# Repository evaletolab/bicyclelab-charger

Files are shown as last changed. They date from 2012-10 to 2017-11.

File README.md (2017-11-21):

# 85-110W single output battery charger

This is an opensource lithium-ion battery charger that use laptop power adapter as input.
* Further reading regarding [the bicycle manager](https://github.com/evaletolab/bicyclelab-manager)?

## Features

1. boost input from 18.5V - 4.7A to 42V (or 47.2V) with ~95% of efficiency 
2. stage charging; current control then voltage control
3. full protections: Short circuit / Overload / Over voltage / Over temperature
4. 1 LED indicator for charging status
5. BMS features; Balancing charge on each cell [TODO]
6. custom number of serial cells 5..12
7. small size, only 30x90x8mm

The PCB board charger v4.2

## The result
8S2P

## Power stage (battery charge)

This if the fourth prototype release. The purpose of this board is to manage the charge  
of a 10/11 serial lithium-ion cell with an input given by a laptop ac adapter (currently the apple magsafe1 85W). 
The software is mainly a PID control based on the MAX_POWER for the fast charge and the BATTERY_VOLTAGE for 
the constant charge. The size of the board is about 30x90mm

## Cell balancing and protection
This project is targeted for each individual cell. The purpose of this project is to make a simple cascading 
module to manage over/under voltage/temperatur for each cell. The first prototype is still not available for testing. 

1. an overvoltage measurement is triggering a passive balancing for the cell
2. TODO - implement an isolated one wire communication to broadcast,
  * undervoltage signal
  * over temperature signal
 
## License
GPL3

Copyright (c) 2012 Olivier Evalet (http://evaletolab.ch/)

Permission is hereby granted, free of charge, to any person obtaining a copy
of this software and associated documentation files (the “Software”), to deal
in the Software without restriction, including without limitation the rights
to use, copy, modify, merge, publish, distribute, sublicense, and/or sell
copies of the Software, and to permit persons to whom the Software is
furnished to do so, subject to the following conditions:

The above copyright notice and this permission notice shall be included in
all copies or substantial portions of the Software.

THE SOFTWARE IS PROVIDED “AS IS”, WITHOUT WARRANTY OF ANY KIND, EXPRESS OR
IMPLIED, INCLUDING BUT NOT LIMITED TO THE WARRANTIES OF MERCHANTABILITY,
FITNESS FOR A PARTICULAR PURPOSE AND NONINFRINGEMENT. IN NO EVENT SHALL THE
AUTHORS OR COPYRIGHT HOLDERS BE LIABLE FOR ANY CLAIM, DAMAGES OR OTHER
LIABILITY, WHETHER IN AN ACTION OF CONTRACT, TORT OR OTHERWISE, ARISING FROM,
OUT OF OR IN CONNECTION WITH THE SOFTWARE OR THE USE OR OTHER DEALINGS IN
THE SOFTWARE.

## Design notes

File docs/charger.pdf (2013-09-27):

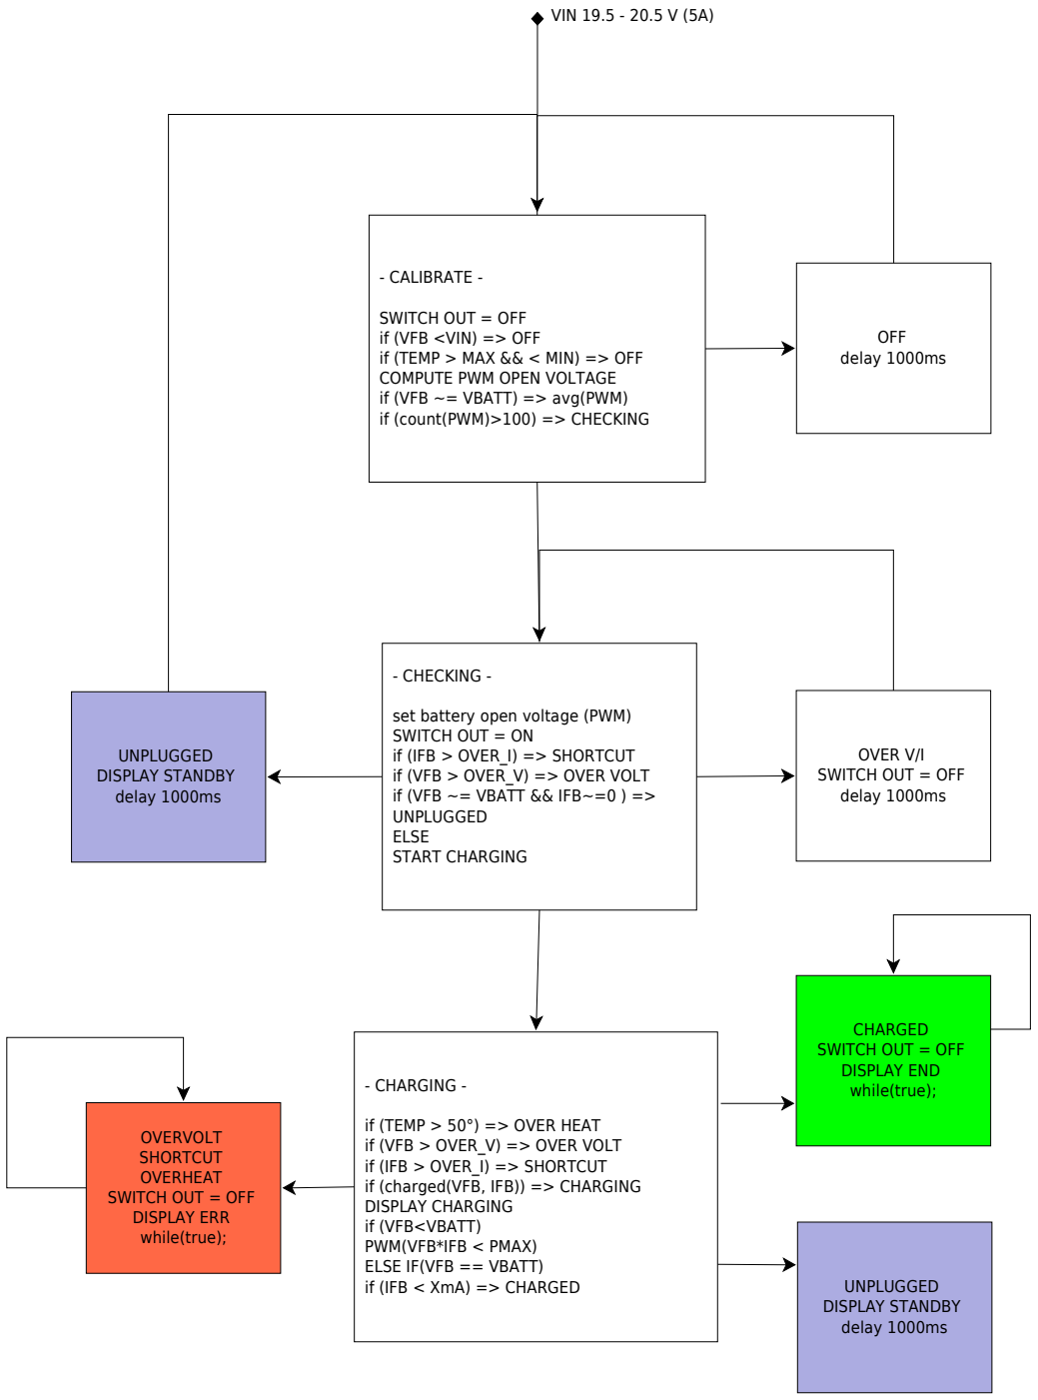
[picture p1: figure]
- CALIBRATE -; SWITCH OUT = OFF if (VFB <VIN) => OFF if (TEMP > MAX && < MIN) => OFF COMPUTE PWM OPEN VOLTAGE if (VFB ~= VBATT) => avg(PWM) if (count(PWM)>100) => CHECKING; OFF delay 1000ms; VIN 19.5 - 20.5 V (5A); - CHECKING -; set battery open voltage (PWM) SWITCH OUT = ON if (IFB > OVER_I) => SHORTCUT if (VFB > OVER_V) => OVER VOLT if (VFB ~= VBATT && IFB~=0 ) => UNPLUGGED ELSE START CHARGING; OVER V/I SWITCH OUT = OFF delay 1000ms; UNPLUGGED DISPLAY STANDBY delay 1000ms; - CHARGING -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

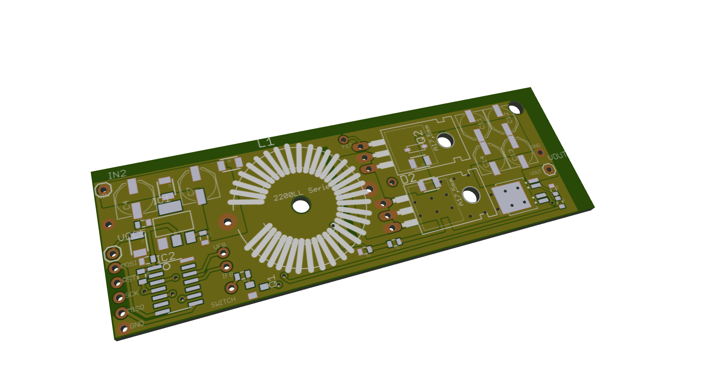
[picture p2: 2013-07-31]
hardware/bicyclelab-charger-v0.1.3d.png

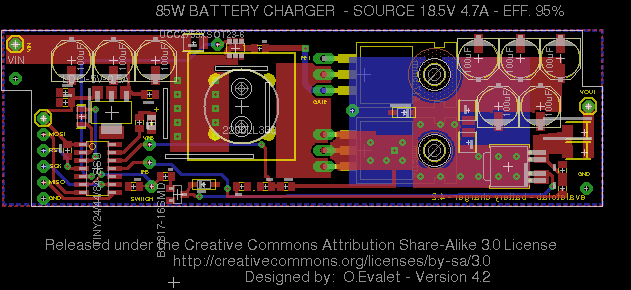
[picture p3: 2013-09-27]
hardware/bicyclelab-charger-v4.2.png

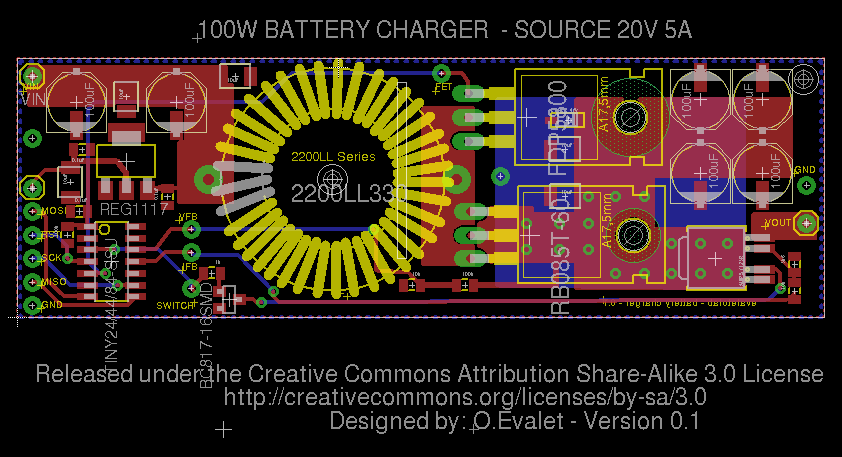
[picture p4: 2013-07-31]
hardware/bicyclelab-charger-v0.1.png

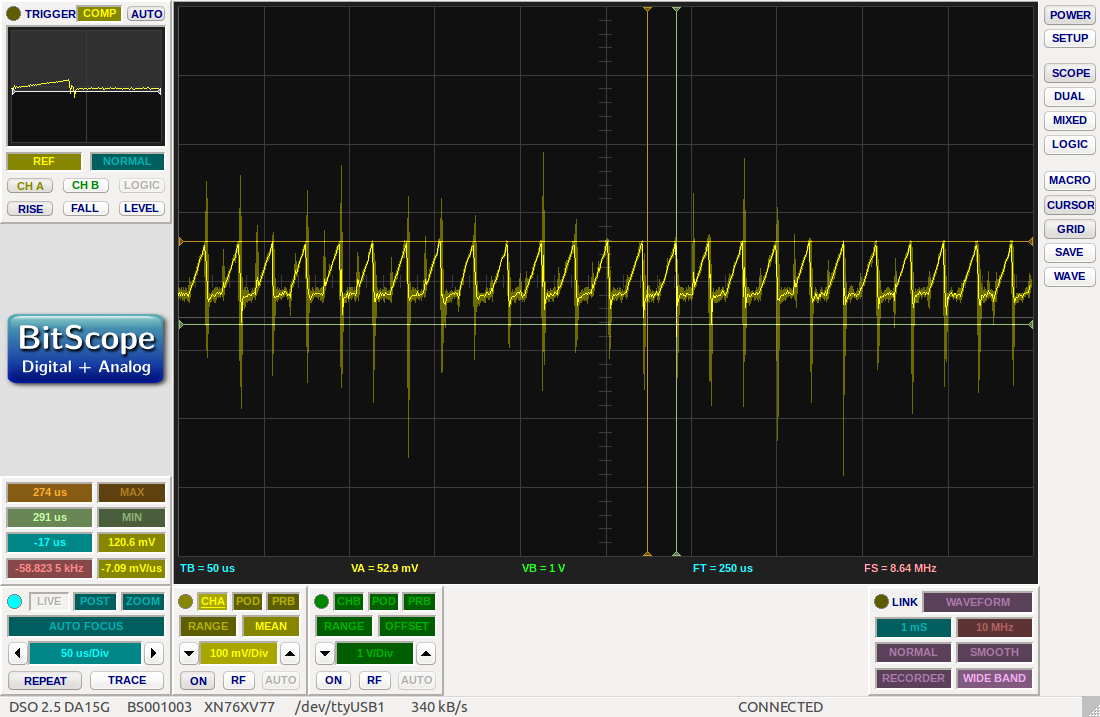
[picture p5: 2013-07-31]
docs/scope/uc1842 - isens - Capture du 2013-07-26 17:00:00.png

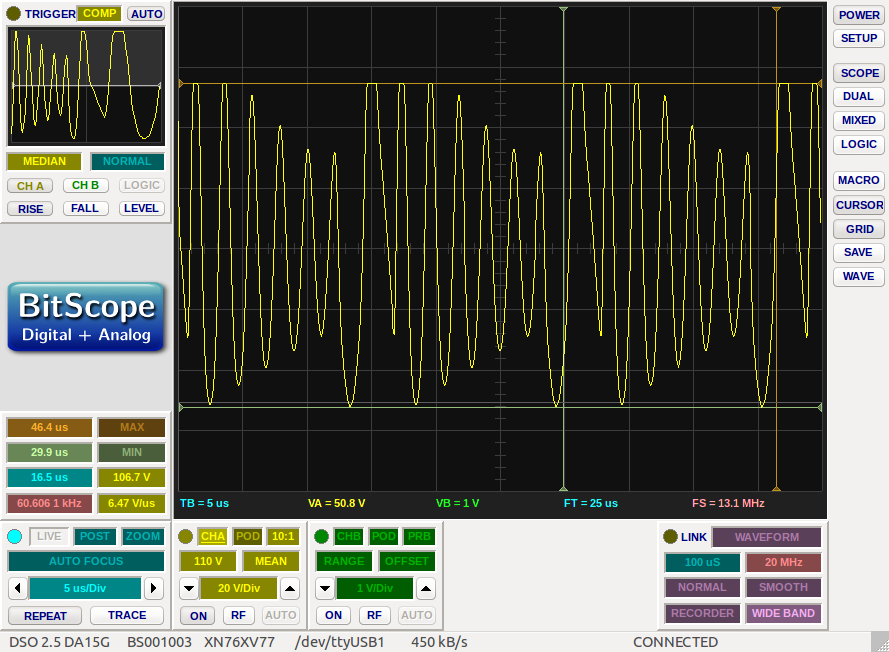
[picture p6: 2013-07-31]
docs/scope/5v - 20V - 60khz - Capture du 2013-07-24 09:50:51.png

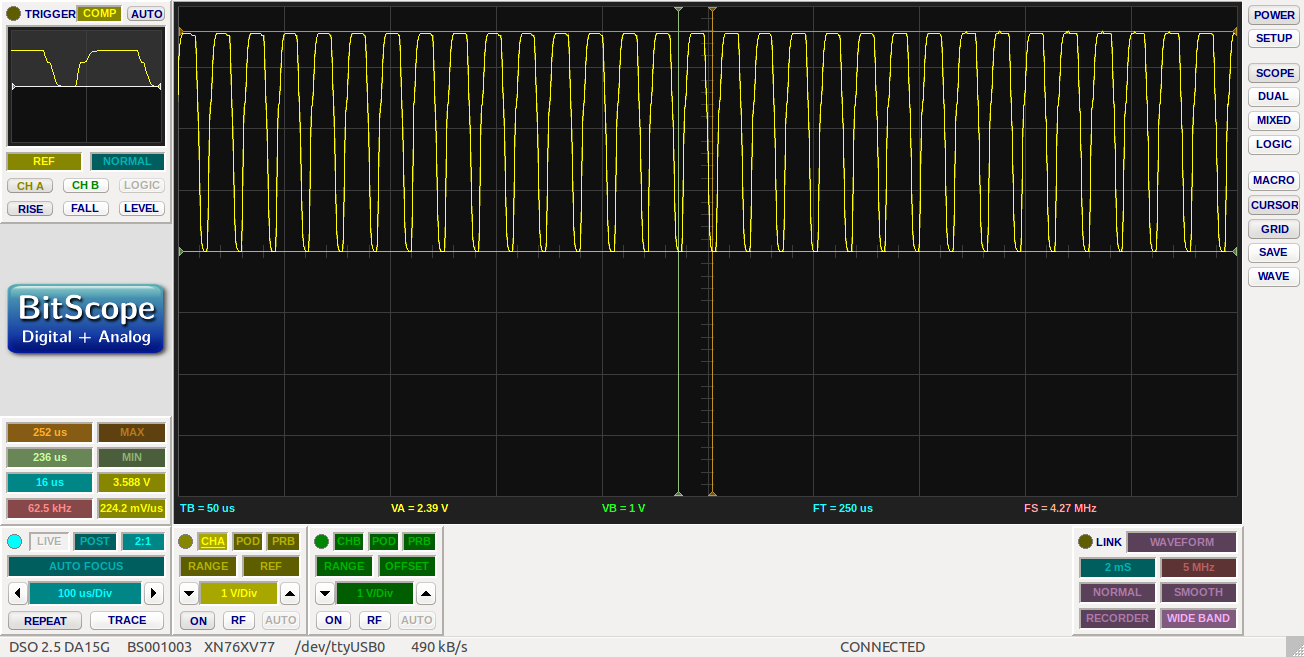
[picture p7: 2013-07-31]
docs/scope/arduino boost - gate - Capture du 2013-07-26 17:20:36.png

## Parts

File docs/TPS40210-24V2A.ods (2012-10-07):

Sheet: 20V_2A
PARAMETER |  | CONDITIONS | MIN | NOM | MAX | UNIT | STATUS
INPUT
Vin | Input voltage |  | 8 | 12 | 14 | V
Iin | Input current |  |  | 4.5 |  | A |  | Vref= | 0.700 V
 | No load I |  |  |  |  | A |  | Pfet< | 0.50 W
UV | Under voltage |  |  | 4.5 |  | V |  | RDSon< | 0.010 Ohms
OUTPUT |  |  |  |  |  |  |  | Rout= | 24.0 Ohms
Vout | Output voltage |  | 23.5 | 24 | 24.5 | V |  | Rout(max)= | 240.0 Ohms
 | Line regulation |  |  |  | 1 % |  |  | Rfb(r4)= | 16'711 Ohms
 | Load regulation |  |  |  | 1 % |  | NOMORE | Risns= | 0.012 Ohms
Vout(ripple) |  |  |  |  | 0.5 | Vpp |  | Rbias(r5)= | 1'535 Ohms
Iout | Output current | 18 =< Vin =< 24 | 0.1 | 1 | 2 | A |  | R7= | 51'100 Ohms
Iocp | Output overcurrent inception point |  | 3.5 |  |  | A |  | RC= | 261K
 | Transiant response |  |  |  |  |  |  | CC= | 100pF
 | Load step |  |  | 1 |  | A | TOFIX | Cout= | 3.6E-05 F
 | Load slew rate |  |  | 1 |  | A/us | TOFIX | C4~ | 63.5E-12 F
 | Overshoot threshold voltage |  |  | 0.5 |  | V | TOFIX | C4> | 12.7E-12 F
OTHER |  |  |  |  |  |  |  | C2= | 3.2E-09 F
Vfd | Diode Forward voltage |  |  | 0.5 |  | V
Fsw | Switching frequency |  |  | 600000 |  | Hz
Vin(ripple) |  |  |  | 0.06 |  | V
Vfb(ref) | Voltage reference for TPS40210 |  |  | 0.7 |  | V
 | Voltage reference for TPS40211 |  |  | 0.26 |  | V
n | Full load efficiency |  |  | 0.95 |  | %
Duty Cycle Estimation Dmin, Dmax |  | Adding 43V zener as secure overvoltage protection BZT52C43
Dmin= | 0.43
Dmax= | 0.67
D= | 0.55
Inductor Selection
Iripple(max)= | 1.05 | NS10155T150MNA (10x10x5.5mm) 15uH (http://ch.mouser.com/ProductDetail/Taiyo-Yuden/NS10155T150MNA/?qs=PzICbMaShUfjlUDrCZqQrFxQdiB4Wjv1sIUX92p1XCQ=) |  | 0.028
Lmin> | 9.5E-06 | IHLP3232DZER150M11 (8x9x4mm) 15uH (http://ch.mouser.com/ProductDetail/Vishay-Dale/IHLP3232DZER150M11/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) |  | 0.000015 |  | uH
L= | 10.0E-06
Iripple(VinTyp)= | 1.10 | IMPORTANT cf. Pfet | DCR(L)= | 0.0124
Iripple(Vinmin)= | 0.90
Ilrms= | 6.14 | WARNING WITH THE INDUCTOR SELECTION
Ilpeak= | 6.57
PL~= | 0.47 | THE SELECTED INDUCTOR DISSIPATES 2.2W OF POWER
Rectifier Diode Selection
Vbrmin= | 30 | the rectifier diode minimum reverse break-down voltage
Id= | 2.00
Idpeak= | 6.57
Pdmax= | 1
Output Capacitor Selection
Cout= | 0.000036 F
ESR= | 0.10 Ohms
R(esr)= | 0.06 Ohms
Input Capacitor Selection
Cin> | 0.000006 F
ESR< | 0.03 Ohms
Current Sense and Current Limit
Riflt= | 1000 Ohm
Ciflt= | 71.4E-12 | For a 1-kΩ filter resistor, 72 pF is calculated and a 100-pF capacitor is selected.
Ciflt= | 100pF
Current Sense Filter
Idrive= | 0.50 A
VISNS= | 0.15 V
Risns< | 0.019 Ohms
Risns< | 0.112 Ohms
Risns= | 0.012 Ohms
Prisns= | 0.305 W
Switching MOSFET Selection |  |  |  |  |  |  |  | FET(check the gate voltage)
Ivdd(max)= | 0.003 | IVDD is the quiescent current of the controller when enabled but not switching in A |  |  |  |  |  | FDS86540 (http://ch.mouser.com/ProductDetail/Fairchild-Semiconductor/FDS86540/) | 60V 20V 18A 5mOhm 5W
Pdiss= | 2.53 W |  |  |  |  |  |  | BSZ076N06NS3 G (http://ch.mouser.com/ProductDetail/Infineon-Technologies/BSZ076N06NS3-G/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) | 60V 20V 7mOhms 60W
Pfet< | 0.71 W | 20 mΩ is calculated to limit the conduction losses to less than .57 mW |  |  |  |  |  | FDMS86520L (http://ch.mouser.com/ProductDetail/Fairchild-Semiconductor/FDMS86520L/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) | 60V 13.2A 8.2mOhms 69W
Pfet= | 0.50 W
Qgs< | 1.3E-08 | Qgs<8,5nF
Rds(on)< | 0.010 Ohms
Feedback Divider Resistors
Vfb= | 0.7
FL(10 % Fsw)= | 30'000 Hz
Rout= | 24.0 Ohms
Rout(max)= | 240.0 Ohms
gm= | 19.19 A/V
Zout= | 0.159 Ohms
Kco= | 3.058
Kcomp= | 0.327
R4(rfb)= | 16'711 Ohms
Cfb= | 3.2E-09
Chf= | 317.47E-13
R5(rbias;r2)= | 1535.2 Ohms
R7(r1)= | 51100.0 Ohms
C2= | 3.17E-09
C2= | 4.7nF
C4~ | 63.5E-12
C4> | 12.7E-12
C4= | 47pF
R-C Oscillator (600Khz)
C3= | 100pF
R6= | 261K
Soft-Start Capacitor
Css= | 240.0E-09
For TSS = 12 ms, CSS = 240 nF. A 220-nF capacitor is selected.
Regulator Bypass
A regulator bypass (BP) capacitor of 1.0-μF is selected per the datasheet recommendation.

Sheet: Feuille2
R5=Rbias
R4=Rfb
C4=Cfb

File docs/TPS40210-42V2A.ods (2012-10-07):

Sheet: 20V_2A
PARAMETER |  | CONDITIONS | MIN | NOM | MAX | UNIT | STATUS | Vclloop(min)= | 0.010 V
INPUT |  |  |  |  |  |  |  | Rcloop= | 0.10 Ohms
Vin | Input voltage |  | 18 | 19 | 20 | V |  | L= | 11.1E-06 H
Iin | Input current |  |  | 5 |  | A |  | Vref= | 0.260 V
 | No load I |  |  |  |  | A |  | Pfet< | 0.50 W
UV | Under voltage |  |  | 4.5 |  | V |  | RDSon< | 0.012 Ohms
OUTPUT |  |  |  |  |  |  |  | Rout= | 21.0 Ohms
Vout | Output voltage |  | 41.5 | 42 | 42.5 | V |  | Rout(max)= | 420.0 Ohms
 | Line regulation |  |  |  | 1 % |  |  | Rfb(r4)= | 24'819 Ohms
 | Load regulation |  |  |  | 1 % |  | NOMORE | Risns= | 0.012 Ohms
Vout(ripple) |  |  |  |  | 0.5 | Vpp |  | Rbias(r5)= | 318 Ohms
Iout | Output current | 18 =< Vin =< 24 | 0.1 | 2 | 2.5 | A |  | R7= | 51'100 Ohms
Iocp | Output overcurrent inception point |  | 3.5 |  |  | A |  | RC= | 261K
 | Transiant response |  |  |  |  |  |  | CC= | 100pF
 | Load step |  |  | 1 |  | A | TOFIX | Cout= | 38.4E-06 F
 | Load slew rate |  |  | 1 |  | A/us | TOFIX | C4~ | 42.8E-12 F
 | Overshoot threshold voltage |  |  | 0.5 |  | V | TOFIX | C4> | 85.5E-13 F
OTHER |  |  |  |  |  |  |  | C2= | 2.1E-09 F
Vfd | Diode Forward voltage |  |  | 0.5 |  | V |  | Cin> | 10.0E-06 F
Fsw | Switching frequency |  |  | 600000 |  | Hz |  | Ciflt= | 88.2E-12 F
Vin(ripple) |  |  |  | 0.06 |  | V |  | Risns= | 0.012 Ohms
Vfb(ref) | Voltage reference for TPS40210 |  |  | 0.7 |  | V
 | Voltage reference for TPS40211 |  |  | 0.26 |  | V
n | Full load efficiency |  |  | 0.95 |  | %
Duty Cycle Estimation Dmin, Dmax |  | Adding 43V zener as secure overvoltage protection BZT52C43
Dmin= | 0.53
Dmax= | 0.58
D= | 0.55
Inductor Selection |  | RLF12560T-100M7R5 (13x13x6mm) 7.8A, DCR=0.0124, 10uH
Iripple(max)= | 1.59375 | NS10155T150MNA (10x10x5.5mm) 4A, DCR=0.028, 15uH
Lmin= | 11.1E-06 | 7447798131 (10x10x6.4mm) 5.2A, DCR=0.022 13uH
L= | 12.0E-06 | CDRH104RNP-120NC (10x10x4mm), 6.5A, DCR=0.04 12uH
Iripple(VinTyp)= | 1.46 |  | DCR(L)= | 0.04
Iripple(Vinmin)= | 1.44
Ilrms= | 5.95 | WARNING WITH THE INDUCTOR SELECTION
Ilpeak= | 6.62
PL~= | 1.41 | THE SELECTED INDUCTOR DISSIPATES 1.4W OF POWER
Rectifier Diode Selection
Vbrmin= | 52.5 | the rectifier diode minimum reverse break-down voltage
Id= | 2.50 | RB095T-40 (45V 6A 0.5V)
Idpeak= | 6.62 | SS5P5-M3/87A (50V 5A 0.69V) SMPC (TO-277A)
Pdmax= | 1.25 | PMEG6030EP,115 (60V 3A 0.53V) SOD-128
 |  | CMSH3-60 (60V 3A .7V) SMC
Output Capacitor Selection
Cout= | 38.4E-06 F
ESR= | 0.11 Ohms
R(esr)= | 0.06 Ohms | 2x20uF 50V Low ESR (<60mOhms) C5750Y5V1H226Z
Input Capacitor Selection
Cin> | 10.0E-06 F | A 10-μF X7R ceramic capacitor is selected.
ESR< | 0.02 Ohms
Current Sense and Current Limit
Riflt= | 1000 Ohm
Ciflt= | 88.2E-12 | For a 1-kΩ filter resistor, 72 pF is calculated and a 100-pF capacitor is selected.
Ciflt= | 100pF
Current Sense Filter
Idrive= | 0.50 A
VISNS= | 0.15 V
Risns< | 0.019 Ohms
Risns< | 0.102 Ohms
Risns= | 0.012 Ohms
Prisns= | 0.245 W
Switching MOSFET Selection |  |  |  |  |  |  |  | FET N-Channel
Ivdd(max)= | 0.003 | IVDD is the quiescent current of the controller when enabled but not switching in A |  |  |  |  |  | FDS86540 (http://ch.mouser.com/ProductDetail/Fairchild-Semiconductor/FDS86540/) | 60V 20V 18A 5mOhm 5W SOIC-8
Pdiss= | 5.53 W |  |  |  |  |  |  | BSZ076N06NS3 G (http://ch.mouser.com/ProductDetail/Infineon-Technologies/BSZ076N06NS3-G/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) | 60V 20V 7mOhms 60W
Pfet< | 2.56 W | 20 mΩ is calculated to limit the conduction losses to less than .57 mW |  |  |  |  |  | FDMS86520L (http://ch.mouser.com/ProductDetail/Fairchild-Semiconductor/FDMS86520L/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) | 60V 13.2A 8.2mOhms 69W
Pfet= | 0.50 W |  |  |  |  |  |  | Si4386DY | 30V 16A 3.1W 7.0mohm@10V
Qgs< | 6.0E-09 | Qgs<8,5nF |  |  |  |  |  | FDS5672
Rds(on)< | 0.012 Ohms
Feedback Divider Resistors
Vfb= | 0.26
FL(10 % Fsw)= | 30'000 Hz
Rout= | 21.0 Ohms
Rout(max)= | 420.0 Ohms
gm= | 13.68 A/V
Zout= | 0.150 Ohms
Kco= | 2.059
Kcomp= | 0.486
R4(rfb)= | 24'819 Ohms
Cfb= | 2.1E-09
Chf= | 213.76E-13
R5(rbias;r2)= | 318.3 Ohms
R7(r1)= | 51100.0 Ohms
C2= | 2.14E-09
C2= | 4.7nF
C4~ | 42.8E-12
C4> | 85.5E-13
C4= | 47pF
R-C Oscillator (600Khz)
C3= | 100pF
R6= | 261K
Soft-Start Capacitor
Css= | 240.0E-09
For TSS = 12 ms, CSS = 240 nF. A 220-nF capacitor is selected.
Regulator Bypass
A regulator bypass (BP) capacitor of 1.0-μF is selected per the datasheet recommendation.

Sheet: 220 adapter
Provider | NAME | MODEL | Vout | Aout | Vripple | Size | Price $
DELL | 90W-AC-ADAPTER | LA90PS0-00 | 19.5 | 4.62 |  | 20 | 20
DELL | 130W-AC-ADAPTER | DA130PE1-00 | 19.5 | 6.7
APPLE | 85W MagSafe Power Adapter

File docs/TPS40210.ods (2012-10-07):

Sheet: 20V_2A
 |  |  |  |  |  |  |  |  |  | 24
 |  |  |  |  |  |  |  |  |  | 67000 | 0.5355150614
 |  |  |  |  |  |  |  |  |  | 225
PARAMETER |  | CONDITIONS | MIN | NOM | MAX | UNIT | STATUS |  |  | 30110
INPUT |  |  |  |  |  |  |  |  |  | 0.36 | 0.7 | 0.252
Vin | Input voltage |  | 18 | 19.5 | 22 | V
Iin | Input current |  |  | 4.5 |  | A
 | No load I |  |  |  |  | A |  | Pfet< | 0.56 W
UV | Under voltage |  |  | 16 |  | V |  | RDSon< | 0.01 Ohms
OUTPUT |  |  |  |  |  |  |  | Rout= | 21.0 Ohms
Vout | Output voltage |  | 41.8 | 42 | 42.8 | V |  | Rfb= | 13294 Ohms
 | Line regulation |  |  |  | 1 % |  |  | Risns= | 0.018 Ohms
 | Load regulation |  |  |  | 1 % |  | NOMORE | Rbias= | 225 Ohms
Vout(ripple) |  |  |  |  | 0.5 | Vpp |  | R 1= | 67000.0 Ohms
Iout | Output current | 18 =< Vin =< 24 | 0.3 | 2 | 2.5 | A |  | RC= | 261K
Iocp | Output overcurrent inception point |  | 3 |  |  | A |  | CC= | 100pF
 | Transiant response
 | Load step |  |  | 1 |  | A | TOFIX
 | Load slew rate |  |  | 1 |  | A/us | TOFIX
 | Overshoot threshold voltage |  |  | 0.5 |  | V | TOFIX
OTHER
Vfd | Diode Forward voltage |  |  | 0.5 |  | V
Fsw | Switching frequency |  |  | 600000 |  | Hz
Vin(ripple) |  |  |  | 0.1 |  | V
Vfb(ref) | Voltage reference for TPS40210 |  |  | 0.7 |  | V
 | Voltage reference for TPS40211 |  |  | 0.26 |  | V
n | Full load efficiency |  |  | 0.95 |  | %
Duty Cycle Estimation Dmin, Dmax |  | Adding 43V zener as secure overvoltage protection BZT52C43
Dmin= | 0.48
Dmax= | 0.58
D= | 0.53
Inductor Selection
Iripple(max)= | 1.1590909091 | NS10155T150MNA (10x10x5.5mm) 15uH (http://ch.mouser.com/ProductDetail/Taiyo-Yuden/NS10155T150MNA/?qs=PzICbMaShUfjlUDrCZqQrFxQdiB4Wjv1sIUX92p1XCQ=) |  | 0.028
Lmin= | 0.0000153 | IHLP3232DZER150M11 (8x9x4mm) 15uH (http://ch.mouser.com/ProductDetail/Vishay-Dale/IHLP3232DZER150M11/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) |  | 0.000015 |  | uH
Iripple(VinTyp)= | 1.15 |  |  | 0.063
Iripple(Vinmin)= | 1.06
Ilrms= | 5.93 | WARNING WITH THE INDUCTOR SELECTION
Ilpeak= | 6.43
PL~= | 2.21 | THE SELECTED INDUCTOR DISSIPATES 2.2W OF POWER
Rectifier Diode Selection
Vbrmin= | 52.5 | the rectifier diode minimum reverse break-down voltage
Id= | 2.50
Idpeak= | 6.43
Pdmax= | 1.25
Output Capacitor Selection
Cout= | 0.000035 F
ESR= | 0.10 Ohms
Input Capacitor Selection
Cin> | 0.000004 F
ESR< | 0.05 Ohms
Current Sense and Current Limit
Riflt= | 1000 Ohm
Ciflt= | 80.4E-12 | For a 1-kΩ filter resistor, 72 nF is calculated and a 100-nF capacitor is selected.
Current Sense Filter
Idrive= | 0.50 A
VISNS= | 0.15 V
Risns< | 0.020 Ohms
Risns< | 0.143 Ohms
Risns= | 0.018 Ohms
Prisns= | 0.335 W
Switching MOSFET Selection |  |  |  |  |  |  |  | FET(check the gate voltage)
Ivdd(max)= | 0.003 | IVDD is the quiescent current of the controller when enabled but not switching in A |  |  |  |  |  | FDS86540 (http://ch.mouser.com/ProductDetail/Fairchild-Semiconductor/FDS86540/) | 60V 20V 18A 5mOhm 5W
Pdiss= | 4.42 W |  |  |  |  |  |  | BSZ076N06NS3 G (http://ch.mouser.com/ProductDetail/Infineon-Technologies/BSZ076N06NS3-G/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) | 60V 20V 7mOhms 60W
Pfet< | 0.56 W | 20 mΩ is calculated to limit the conduction losses to less than .57 mW |  |  |  |  |  | FDMS86520L (http://ch.mouser.com/ProductDetail/Fairchild-Semiconductor/FDMS86520L/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) | 60V 13.2A 8.2mOhms 69W
Qgs< | 8.3E-09 | Qgs<8,5nF
Rds(on)< | 0.01 Ohms
Feedback Divider Resistors
Vfb= | 0.7
FL(10 % Fsw)= | 30'000 Hz
Rout= | 21.0 Ohms
gm= | 23.54 A/V
Zout= | 0.214 Ohms
Kco= | 5.040
Kcomp= | 0.198
R4(rfb)= | 13294 Ohms
Cfb= | 4.0E-09
Chf= | 39.91E-12
R5(rbias;r2)= | 225 Ohms
R7(r1)= | 67000.0 Ohms
C2= | 3.99E-09
C2= | 4.7nF
C4~ | 79.8E-12
C4> | 16.0E-12
C4= | 47pF
R-C Oscillator (600Khz)
C3= | 100pF
R6= | 261K
Soft-Start Capacitor
Css= | 240.0E-09
For TSS = 12 ms, CSS = 240 nF. A 220-nF capacitor is selected.
Regulator Bypass
A regulator bypass (BP) capacitor of 1.0-μF is selected per the datasheet recommendation.

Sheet: Feuille2
R5=Rbias
R4=Rfb
C4=Cfb

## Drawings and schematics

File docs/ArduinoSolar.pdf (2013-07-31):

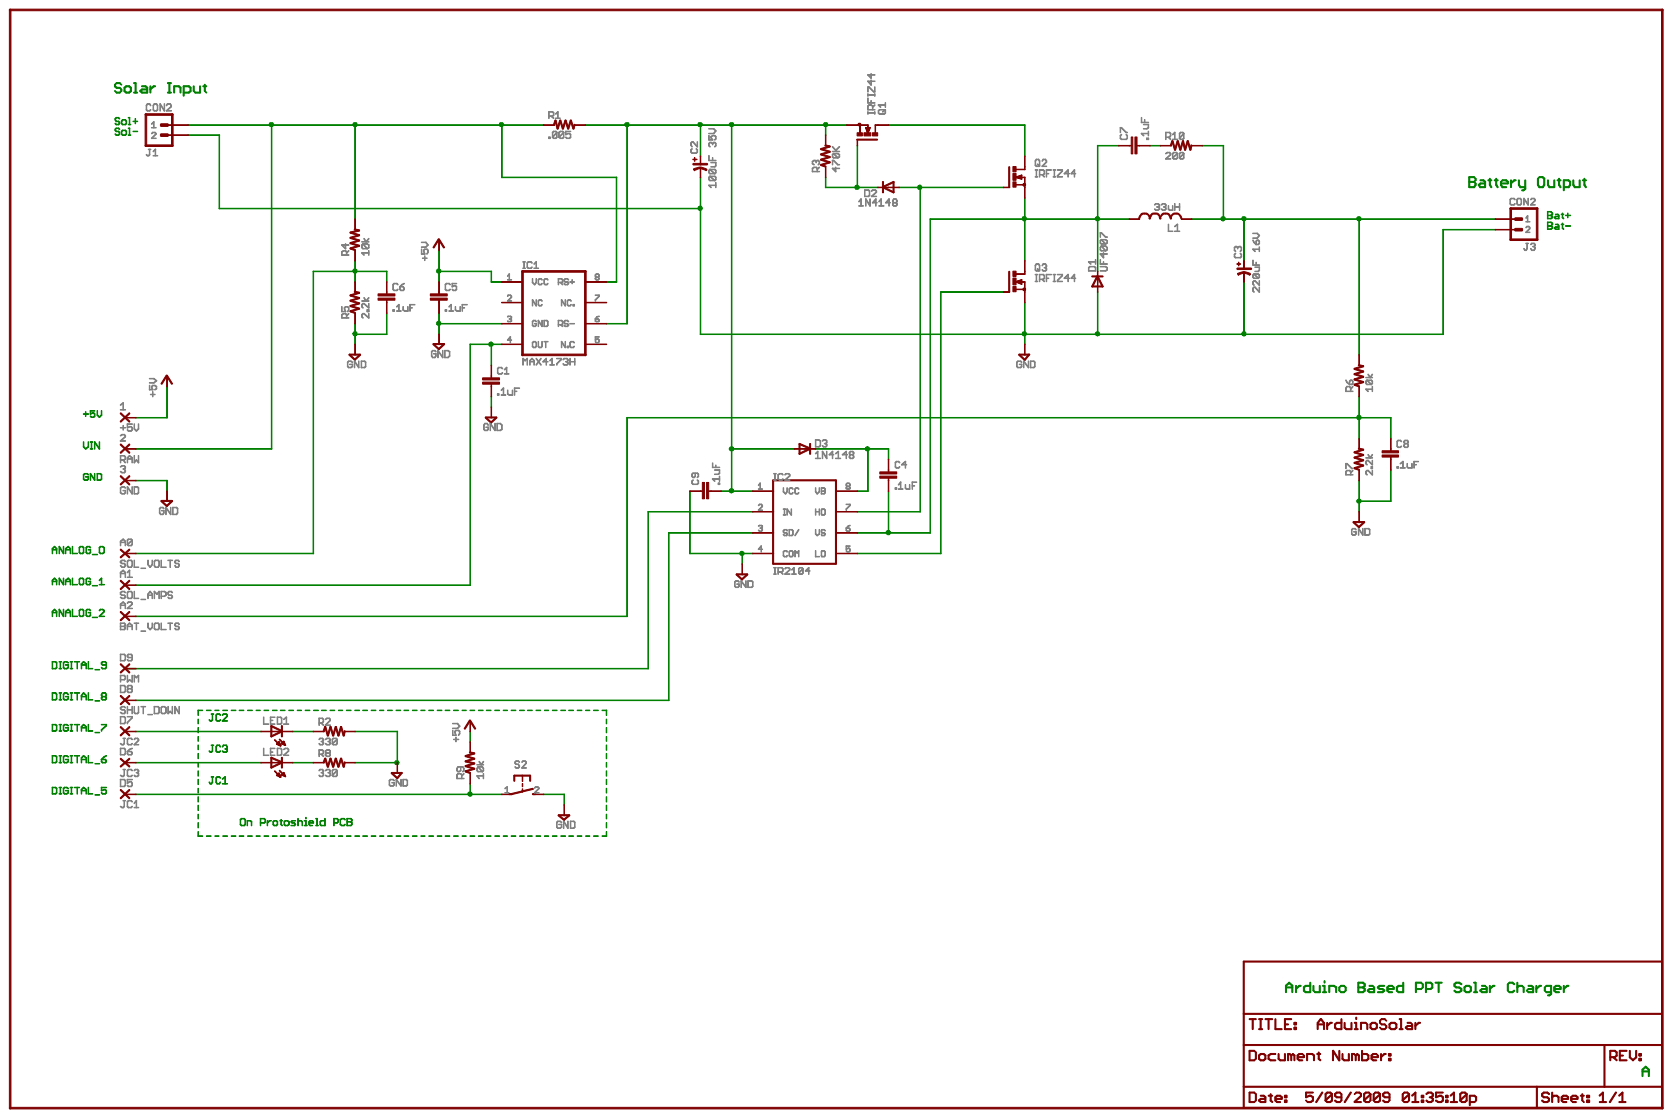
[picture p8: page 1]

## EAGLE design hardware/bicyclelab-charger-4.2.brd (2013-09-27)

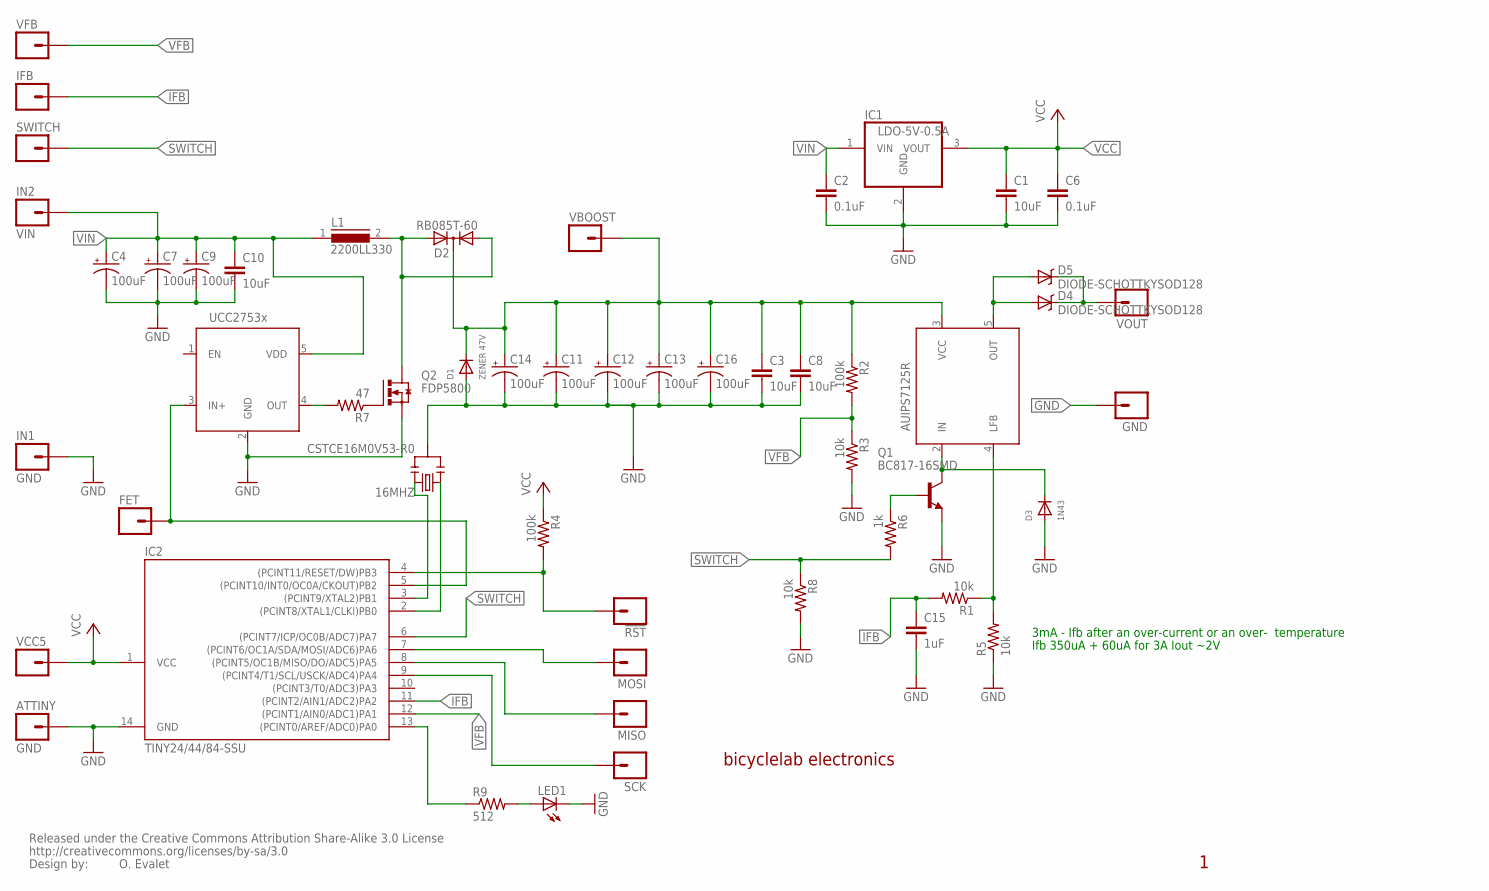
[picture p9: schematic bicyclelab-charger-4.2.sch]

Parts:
16MHZ: CSTCE16M0V53-R0; RESONATOR-SMD
!RST: M01SMDNS; 1X01NS
ATTINY: GND; 1X01NS
C1: 10uF; 0805
C2, C6: 0.1uF; 0805
C3, C8, C10: 10uF; 1210
C4, C7, C9, C11, C12, C13, C14, C16: 100uF; PANASONIC_D
C15: 1uF; 0805
D1: ZENER 47V; SOD-123
D2: RB085T-60; TO220AB
D3: 1N43; SOD-123
D4, D5: DIODE-SCHOTTKYSOD128; SOD-128
FET: M01SMDNS; 1X01NS
GND: M01SMDNS; 1X01NS
IC1: LDO-5V-0.5A; SOT223
IC2: TINY24/44/84-SSU; SOIC14
IFB: M01SMDNS; 1X01NS
IN1: GND; 1X01NS
IN2: VIN; 1X01
L1: 2200LL330; DR175
LED1: LEDCHIP-LED0805; CHIP-LED0805
MISO: M01SMDNS; 1X01NS
MOSI: M01SMDNS; 1X01NS
Q1: BC817-16SMD; SOT23-BEC
Q2: FDP5800; TO220AH
R1, R3, R5, R8: 10k; 0805
R2, R4: 100k; 0805
R6: 1k; 0805
R7: 47; 0805
R9: 512; 0805
SCK: M01SMDNS; 1X01NS
SWITCH: M01SMDNS; 1X01NS
U$1: UCC2753XSOT23-6; SOT23-6
U$5: CREATIVE_COMMONS
U$8: AUIPS7125R; DPAK-5
VBOOST: M01SMDNS; 1X01NS
VCC5: M01PTH; 1X01
VFB: M01SMDNS; 1X01NS
VOUT: M01PTH; 1X01

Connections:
GND: 16MHZ.2, ATTINY.1, C1.2, C2.2, C3.2, C4.-, C6.2, C7.-, C8.2, C9.-, C10.2, C11.-, C12.-, C13.-, C14.-, C15.2, C16.-, D1.A, D3.A, GND.1, IC1.2 (GND), IC2.14 (GND), IN1.1, LED1.C, Q1.E, Q2.E (S), R3.2, R5.1, R8.2, U$1.2 (GND)
IFB: C15.1, IC2.11 ((PCINT2/AIN1/ADC2)PA2), IFB.1, R1.2
unnamed: FET.1, IC2.5 ((PCINT10/INT0/OC0A/CKOUT)PB2), U$1.3 (IN+)
unnamed: Q1.B, R6.1
unnamed: !RST.1, IC2.4 ((PCINT11/RESET/DW)PB3), R4.2
unnamed: Q2.B (G), R7.1
unnamed: IC2.7 ((PCINT6/OC1A/SDA/MOSI/ADC6)PA6), MOSI.1
unnamed: IC2.8 ((PCINT5/OC1B/MISO/DO/ADC5)PA5), MISO.1
unnamed: IC2.9 ((PCINT4/T1/SCL/USCK/ADC4)PA4), SCK.1
unnamed: D4.1 (C), D5.1 (C), VOUT.1
unnamed: R1.1, R5.2, U$8.4 (LFB)
unnamed: D3.C, Q1.C, U$8.2 (IN)
unnamed: LED1.A, R9.2
unnamed: IC2.13 ((PCINT0/AREF/ADC0)PA0), R9.1
unnamed: R7.2, U$1.4 (OUT)
unnamed: 16MHZ.3, IC2.3 ((PCINT9/XTAL2)PB1)
unnamed: 16MHZ.1, IC2.2 ((PCINT8/XTAL1/CLKI)PB0)
SWITCH: IC2.6 ((PCINT7/ICP/OC0B/ADC7)PA7), R6.2, R8.1, SWITCH.1
VBOOST: C3.1, C8.1, C11.+, C12.+, C13.+, C14.+, C16.+, D1.C, D2.C, R2.1, U$8.3 (VCC), VBOOST.1
VCC: C1.1, C6.1, IC1.3 (VOUT), IC2.1 (VCC), R4.1, VCC5.1
VFB: IC2.12 ((PCINT1/AIN0/ADC1)PA1), R2.2, R3.1, VFB.1
VFET: D2.A1, D2.A2, L1.2, Q2.C (D)
VIN: C2.1, C4.+, C7.+, C9.+, C10.1, IC1.1 (VIN), IN2.1, L1.1, U$1.5 (VDD)
VOUT: D4.2 (A), D5.2 (A), U$8.5 (OUT)

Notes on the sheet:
bicyclelab electronics
O. Evalet
3mA - Ifb after an over-current or an over- temperature
Ifb 350uA + 60uA for 3A Iout ~2V

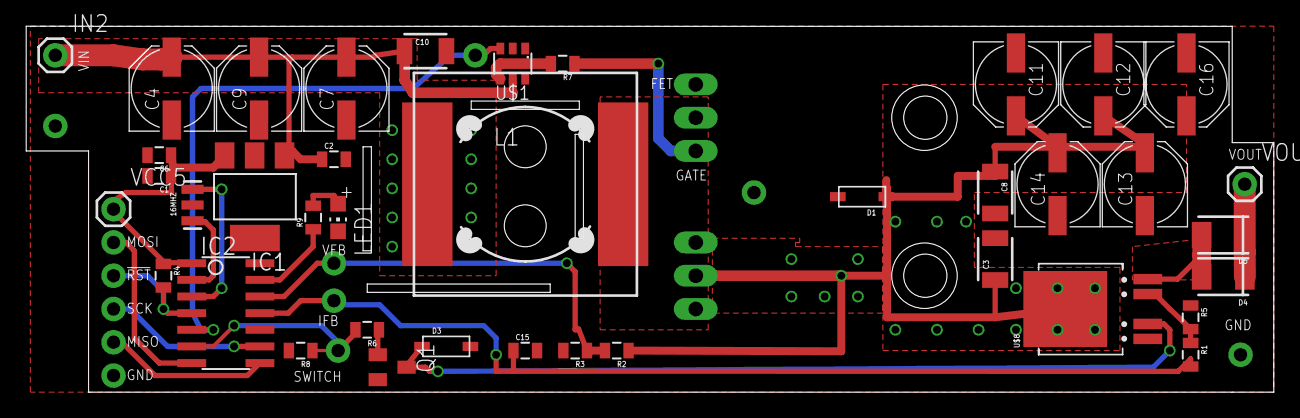
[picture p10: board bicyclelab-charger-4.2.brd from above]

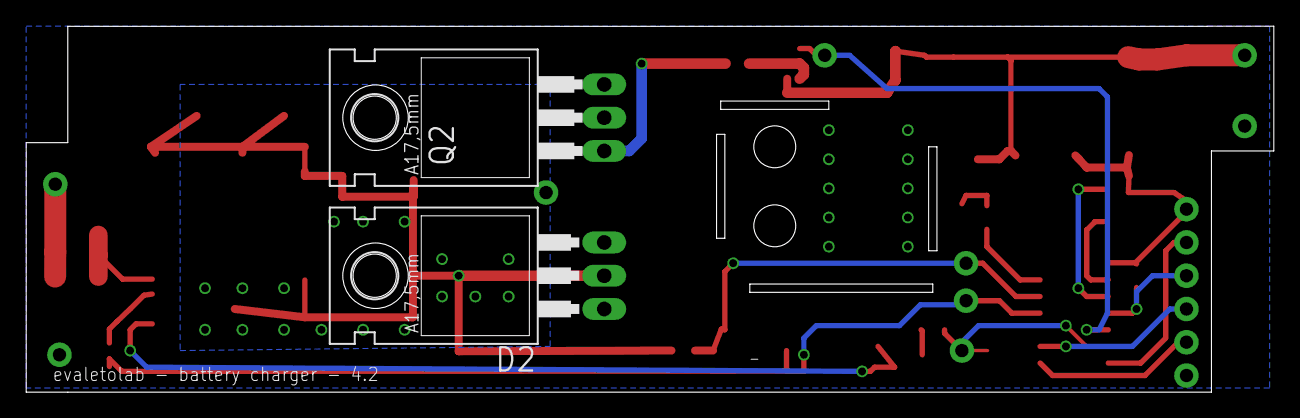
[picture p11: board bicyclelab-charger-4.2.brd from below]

Board: 2 copper layers, 95.2 x 27.9 mm, 54 parts (2 on the bottom side), 24 nets.

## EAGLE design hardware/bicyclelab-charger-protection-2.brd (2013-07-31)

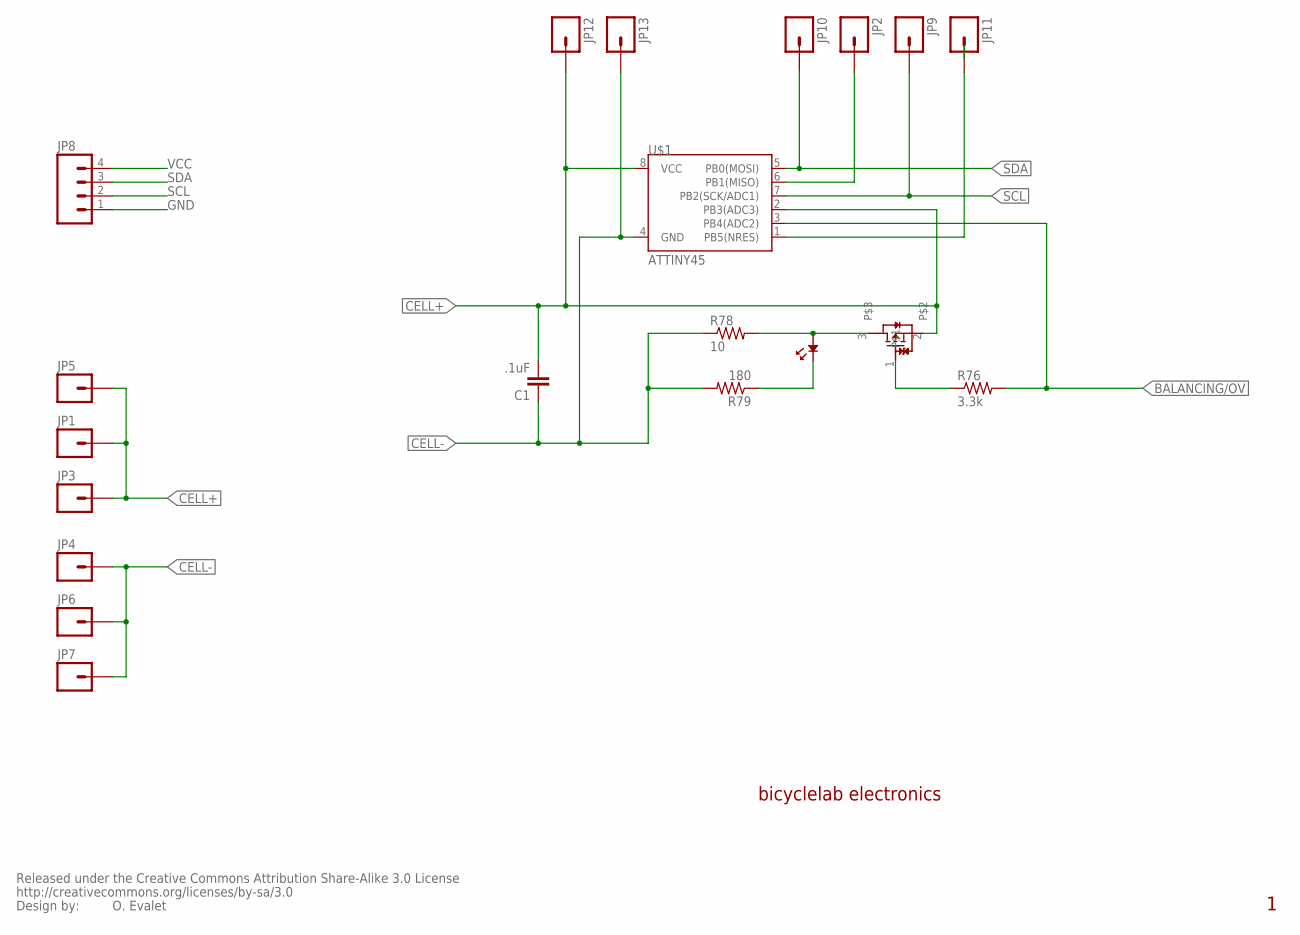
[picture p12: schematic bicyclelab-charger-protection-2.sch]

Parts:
C1: .1uF; C0402
JP1, JP3, JP4, JP5, JP6, JP7: M01SMD-4.5X1.5; PAD-1.5X4.5
JP2, JP9, JP10, JP11, JP12, JP13: M01SMD-TINY; PAD-SMD
JP8: M04PTH; 1X04
LED12: LED-0805; 0805
R76: 3.3k; R0805
R78: 10; R2512
R79: 180; R0805
T12: RTR020P02; TSMT3
U$1: ATTINY45; SO08-EIAJ
U$5: CREATIVE_COMMONS

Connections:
BALANCING/OV: R76.2, U$1.3 (PB4(ADC2))
CELL+: C1.2, JP1.P$1, JP3.P$1, JP5.P$1, JP12.P$1, T12.2, U$1.2 (PB3(ADC3)), U$1.8 (VCC)
CELL-: C1.1, JP4.P$1, JP6.P$1, JP7.P$1, JP13.P$1, R78.1, R79.2, U$1.4 (GND)
GND: JP8.1
unnamed: JP2.P$1, U$1.6 (PB1(MISO))
unnamed: JP11.P$1, U$1.1 (PB5(NRES))
unnamed: LED12.P$2, R78.2, T12.3
unnamed: LED12.P$1, R79.1
unnamed: R76.1, T12.1
SCL: JP8.2, JP9.P$1, U$1.7 (PB2(SCK/ADC1))
SDA: JP8.3, JP10.P$1, U$1.5 (PB0(MOSI))
VCC: JP8.4

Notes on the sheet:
bicyclelab electronics
O. Evalet

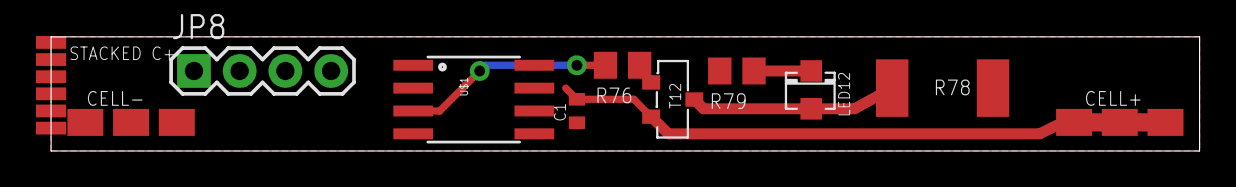
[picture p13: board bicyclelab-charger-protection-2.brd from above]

Board: 2 copper layers, 63.8 x 6.3 mm, 21 parts (0 on the bottom side), 10 nets.

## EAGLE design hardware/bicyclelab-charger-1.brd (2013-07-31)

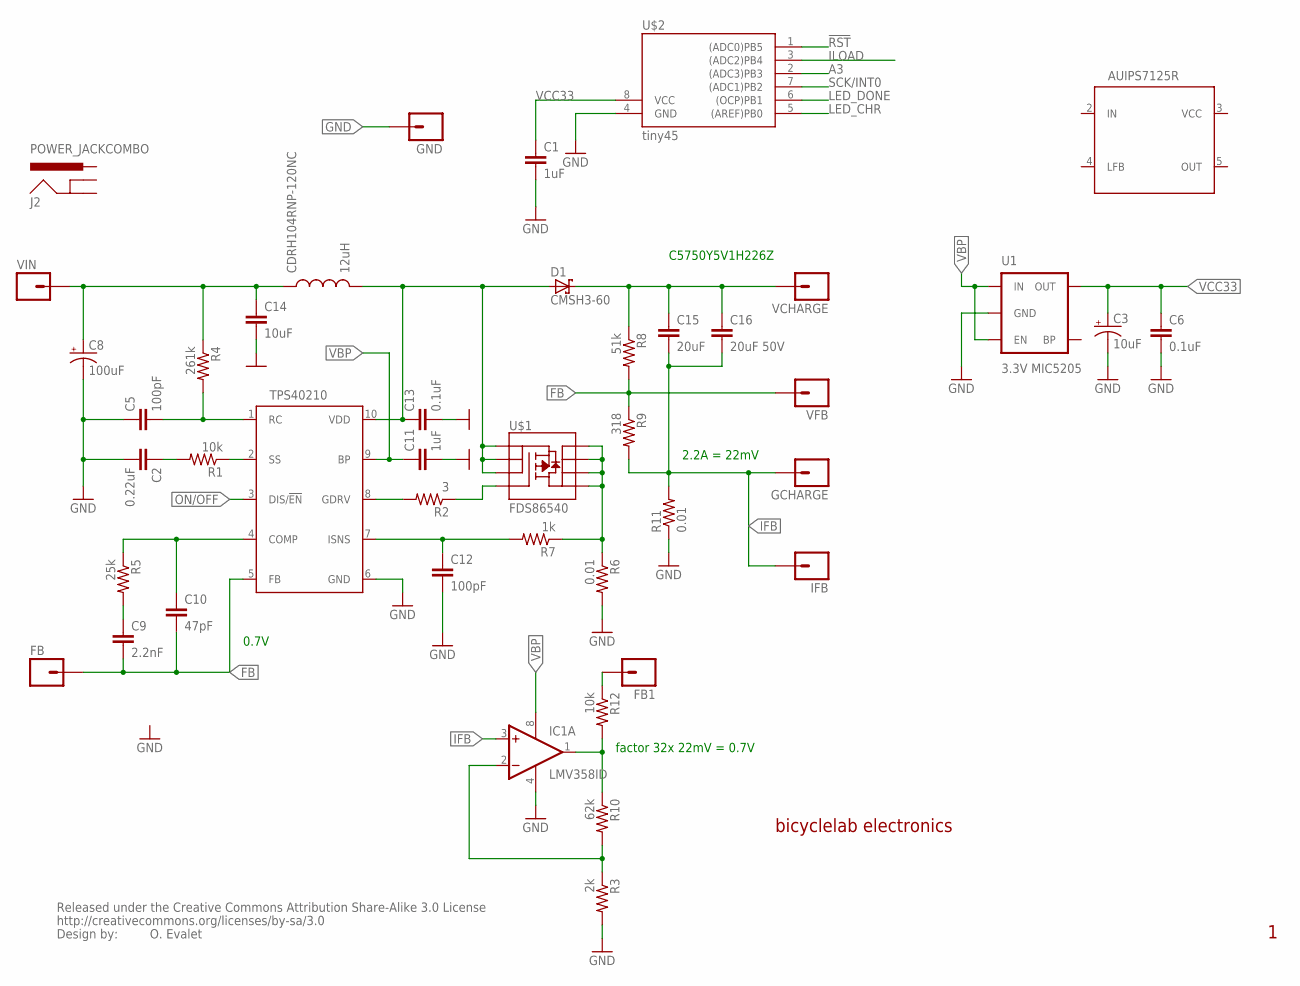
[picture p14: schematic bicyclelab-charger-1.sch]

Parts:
11: TPS40211; MSOP-10-GNDPAD
C1, C11: 1uF; 0402-CAP
C2: 0.22uF; 0402-CAP
C3: 10uF; EIA3216
C5, C12: 100pF; 0402-CAP
C6: 0.1uF; 0603-CAP
C8: 100uF; PANASONIC_C
C9: 2.2nF; 0402-CAP
C10: 47pF; 0402-CAP
C13: 0.1uF; 0402-CAP
C14: 10uF; 1206
C15: 20uF; C2220K
C16: 20uF 50V; C2220K
CDRH104RNP-120NC: 12uH; CR75
D1: CMSH3-60; SMC
FB, FB1: M01SMDNS; 1X01NS
GCHARGE: M01SMDNS; 1X01NS
GND: M01SMDNS; 1X01NS
IC1: LMV358ID; SO08
IFB: M01SMDNS; 1X01NS
J2: POWER_JACKCOMBO; POWER_JACK_COMBO
R1, R12: 10k; 0402-RES
R2: 3; 0402-RES
R3: 2k; 0402-RES
R4: 261k; 0402-RES
R5: 25k; 0402-RES
R6, R11: 0.01; 0402-RES
R7: 1k; 0402-RES
R8: 51k; 0402-RES
R9: 318; 0402-RES
R10: 62k; 0402-RES
U1: 3.3V MIC5205; SOT23-5
U$1: FDS86540; SO08
U$2: tiny45; SOIC8
U$5: CREATIVE_COMMONS
U$8: AUIPS7125R; DPAK-5
VCHARGE: M01SMDNS; 1X01NS
VFB: M01SMDNS; 1X01NS
VIN: M01SMDNS; 1X01NS

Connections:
!RST: U$2.1 ((ADC0)PB5)
A3: U$2.2 ((ADC3)PB3)
FB: 11.5 (FB), C9.2, C10.2, FB.1, R8.2, R9.1, VFB.1
FB1: IC1.1 (OUT), R10.1, R12.2
GND: 11.6 (GND), C1.2, C2.2, C3.C (-), C5.1, C6.2, C8.-, C11.2, C12.2, C13.2, C14.2, GND.1, IC1.4 (V-), R3.2, R6.2, R11.1, U1.2 (GND), U$2.4 (GND)
IFB: C15.2, C16.2, GCHARGE.1, IC1.3 (+IN), IFB.1, R9.2, R11.2
ILOAD: U$2.3 ((ADC2)PB4)
LED_CHR: U$2.5 ((AREF)PB0)
LED_DONE: U$2.6 ((OCP)PB1)
unnamed: C8.+, C14.1, CDRH104RNP-120NC.P$1 (1), R4.1, VIN.1
unnamed: 11.1 (RC), C5.2, R4.2
unnamed: 11.2 (SS), R1.1
unnamed: C2.1, R1.2
unnamed: R2.1, U$1.4 (G)
unnamed: C15.1, C16.1, D1.C, R8.1, VCHARGE.1
unnamed: 11.8 (GDRV), R2.2
unnamed: 11.4 (COMP), C10.1, R5.1
unnamed: C9.1, R5.2
unnamed: FB1.1, R12.1
unnamed: 11.10 (VDD), C13.1, CDRH104RNP-120NC.P$2 (2), D1.A, U$1.1 (S), U$1.2 (S), U$1.3 (S)
unnamed: R6.1, R7.1, U$1.5 (D), U$1.6 (D), U$1.7 (D), U$1.8 (D)
unnamed: 11.7 (ISNS), C12.1, R7.2
unnamed: IC1.2 (-IN), R3.1, R10.2
ON/OFF: 11.3 (DIS/!EN)
SCK/INT0: U$2.7 ((ADC1)PB2)
VBP: 11.9 (BP), C11.1, IC1.8 (V+), U1.1 (IN), U1.3 (EN)
VCC33: C1.1, C3.A (+), C6.1, U1.5 (OUT), U$2.8 (VCC)

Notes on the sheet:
bicyclelab electronics
O. Evalet
C5750Y5V1H226Z
0.7V
2.2A = 22mV
factor 32x 22mV = 0.7V

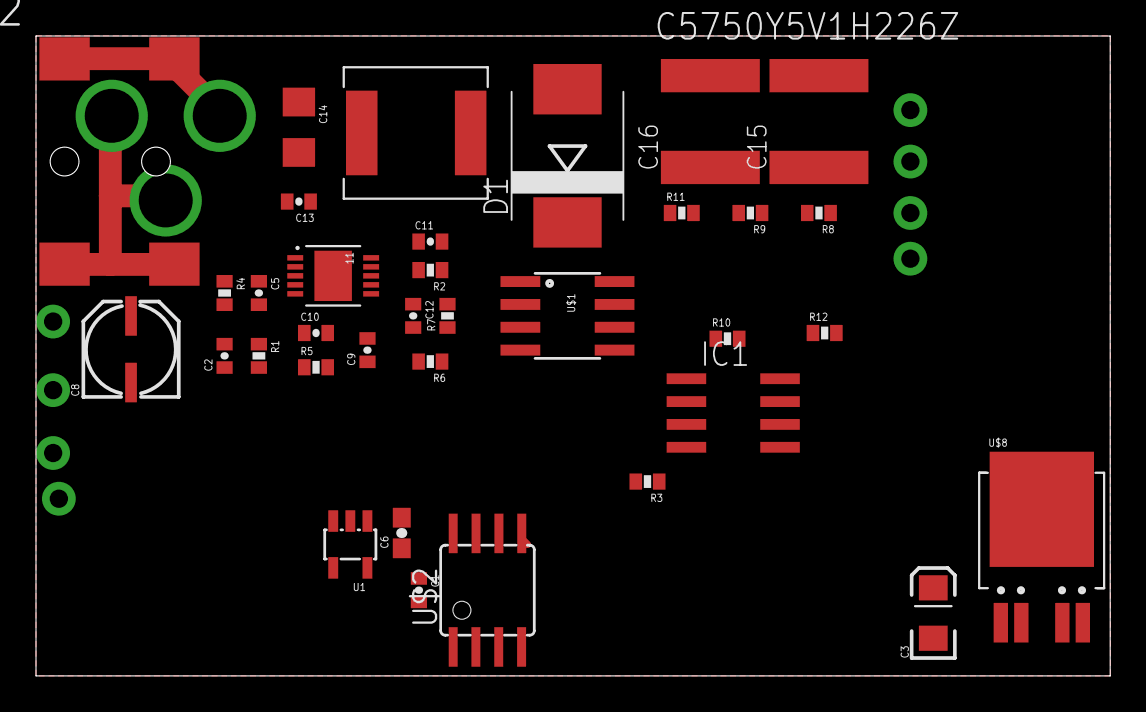
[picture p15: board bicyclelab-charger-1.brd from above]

Board: 2 copper layers, 59.7 x 35.5 mm, 44 parts (0 on the bottom side), 20 nets.

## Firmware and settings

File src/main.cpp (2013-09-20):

/**
 * read value from cell, balance if needed, inform the status 
 *  roadmap:
 *  - read value from cell
 *  - get status from stacked cell
 *  - set status from next cell
 * 
 *  
 */

#ifdef ARDUINO
# include <Arduino.h>
#else
# include <WProgram.h>
#endif
#include "config.h"
#include "energy.h"
#include "charger.h"
#ifdef TINY
#include <core_timers.h>
#endif

#ifdef CONFIG_WITH_EEPROM
//#include <EEPROM.h>
#endif



#ifdef CONFIG_WITH_ECLIPSE
extern "C" void __cxa_pure_virtual() {  }
#endif

static CHARGER charger;


void setup()   {                

  //
  //pullup the AD   
  pinMode(A_VFB, INPUT);
  digitalWrite(A_VFB, HIGH);

  pinMode(A_IFB, INPUT);
  digitalWrite(A_IFB, HIGH);

  //pulldown pwm
  pinMode(P_PWM, OUTPUT);
  analogWrite(P_PWM,0);  
  
  
  pinMode(P_VCC5, INPUT);
  digitalWrite(P_VCC5, HIGH);
  
  //
  // charger is on
  pinMode(P_SW, OUTPUT);
  digitalWrite(P_SW, LOW);

#ifdef TINY
  //
  // setup timer to the maximum speed at 52Khz  
  OSCCAL = 0xFF;  
  Timer1_SetWaveformGenerationMode(Timer1_Fast_PWM_FF);
  Timer1_ClockSelect(Timer1_Prescale_Value_1);
#else 
  // http://arduino.cc/en/Tutorial/SecretsOfArduinoPWM
  // Set pin 6's PWM frequency to 62500 Hz (62500/1 = 62500)
  // Note that the base frequency for pins 5 and 6 is 62500 Hz  
  // *   - Changes on pins 3, 5, 6, or 11 may cause the delay() and
  // *     millis() functions to stop working. Other timing-related
  // *   - Pins 5 and 6 are paired on timer0
  // *   - Pins 9 and 10 are paired on timer1
  // *   - Pins 3 and 11 are paired on timer2
  TCCR0B = TCCR0B & 0b11111000 | 0x01;
#endif
   
  
  charger_init(charger);

#ifdef CONFIG_WITH_PRINT
  Serial.begin(115200);
	Serial.println("Booting ");
#endif

}

void loop(){	
  //
  //
  // checking when output is switched off
  // detect internal issue like undervoltage, over current, over temperature 
  // or unplugged input (for debug only)
  if(!charger_openvoltage(charger)) 
    return;


  // Checking battery
  // ================
  // 1)The charger check if a battery is plugged, we assume that battery capacity 
  //   and voltage are hardcoded ( SmartBattery feature is not yet implemented)
  // 2)The charger then checks for over/under battery temperature and over voltage 
  //   and flags an error if any of these are detected, 
  //   -> sending a short error message to the PC.   
  //
  // ----
  // http://batteryuniversity.com/learn/article/charging_lithium_ion_batteries
  // Do not recharge lithium-ion if a cell has stayed at or below 1.5V for more 
  // than a week. Copper shunts may have formed inside the cells that can lead 
  // to a partial or total electrical short. If recharged, the cells might become 
  // unstable, causing excessive heat or showing other anomalies. Li-ion packs 
  // that have been under stress are more sensitive to mechanical abuse, such 
  // as vibration, dropping and exposure to heat.
  if(!charger_checking(charger)) 
    return;

#ifdef CONFIG_WITH_PRINT      
      Serial.print("2 OK ");
      Serial.print(" PWM: ");Serial.print(charger.pwm,2);
      Serial.print(" I: ");Serial.print(charger.ifb*I_FACTOR,2);
      Serial.print(" V: ");Serial.println(charger.vfb*V_FACTOR,2);
#endif      
  
  //
  // main loop, charging (never exit function!)
  // ==========================================
  // During all loop (fast & constant charge) the charger check 
  // the temperature and if battery is hot unplugged
  //
  // 2)If OK control proceeds to the Constant Current loop where the PWM signal 
  //   on-time is adjusted up or down until the measured current matches the 
  //   specified fast charge current. 
  //   -> The charge LED flashes quickly during this mode.
  //
  // 3)When the Maximum Charge Voltage setting is reached then the 
  //   mode switches to Constant Voltage and a new loop is entered that uses 
  //   the same method as above to control voltage at the Maximum Charge 
  //   Voltage point. 
  //   -> The LED now flashes more slowly. 
  //
  //   This continues until 30 minutes after the charge current, which is 
  //   decreasing with time in constant voltage mode, reaches the minimum 
  //   (set at 50 mA per 1600 mAH of capacity). 
  //   ->The charger then shuts off and the LED goes on steady.
  // 
  //
  charger_mainloop(charger);
  
#ifdef CONFIG_WITH_PRINT      
      Serial.print("3 OK ");
      Serial.print(" PWM: ");Serial.print(charger.pwm,2);
      Serial.print(" I: ");Serial.print(charger.ifb*I_FACTOR,2);
      Serial.print(" V: ");Serial.println(charger.vfb*V_FACTOR,2);
#endif      
  while(true);
}

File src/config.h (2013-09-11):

/**
 * battery life calculator
 * http://oregonembedded.com/batterycalc.htm
 */

#ifndef CONFIG_H_
#define CONFIG_H_

#define CONFIG_WITH_DEBUG
#define CONFIG_WITH_I2C
#define CONFIG_WITH_ECLIPSE
//#define CONFIG_WITH_LOGGER
//#define CONFIG_WITH_TIMER

// divide clock
#if F_CPU == 16000000L
#	define SET_PRESCALER 1
#elif F_CPU == 8000000L
#	define SET_PRESCALER 0
#endif

// Disabled EEPROM when debugging
// DEBUG CHANNEL ATTINYX5,
// if (F_CPU <= 8000000L) => port B bit 3 (PB3:4) ELSE port B bit 2 (PB2:5)
// DEBUG CHANNEL ATTINYX4,
// if (F_CPU <= 8000000L) => port B bit 0 (PB0:2) ELSE port A bit 0 (PA0:13)
#ifdef DEBUG_SERIAL
#  define CONFIG_WITH_PRINT
#else
#	define CONFIG_WITH_EEPROM
#endif

#define         PRINT_TICK 200
#define         TIMER_TICK 10
#define         TIMER_WAIT 100000/2
#define         PRINT 1

#define  V2B(V)  (V*1023.0/VCC_REF)


#if defined( __AVR_ATtinyX4__ )


// ATMEL ATTINY84 / ARDUINO
//
//                           +-\/-+
//                     VCC  1|    |14  GND
//  (Serial1)  (D  0)  PB0  2|    |13  AREF (D 10)       (Serial2)
//             (D  1)  PB1  3|    |12  PA1  (D  9) 
//                     PB3  4|    |11  PA2  (D  8) 
//  PWM  INT0  (D  2)  PB2  5|    |10  PA3  (D  7) 
//  PWM        (D  3)  PA7  6|    |9   PA4  (D  6) 
//  PWM        (D  4)  PA6  7|    |8   PA5  (D  5)        PWM (Serial3)
//                           +----+


#define         P_PWM 5
#define         P_SW 6
#define         P_VCC5 7
#define         A_VFB 1
#define         A_IFB 2

#define TEMPERATURE_CALIBRATE 294

// 0x22 => TEMP sensor, 0x80 1.1V reference
# define A_TEMP 0xA2
//1.1V VREF MUX100001
# define MUX_VREF 0b00100001
//VCC as voltage reference _BT(REFS0)
# define ADC_VREF 0b00000000

#elif defined( __AVR_ATtinyX5__ )

// ATMEL ATTINY45 / ARDUINO
//
//                           +-\/-+
//  Ain0 !RST  (D  5)  PB5  1|    |8   VCC
//  Ain3       (D  3)  PB3  2|    |7   PB2  (D  2)  INT0  Ain1 SCK
//  Ain2       (D  4)  PB4  3|    |6   PB1  (D  1)        pwm1 MISO
//                     GND  4|    |5   PB0  (D  0)        pwm0 MOSI
//                           +----+


#define TEMPERATURE_CALIBRATE 294
// 0x0F => TEMP sensor, 0x80 1.1V reference
# define A_TEMP 0x8F
//1.1V VREF
# define MUX_VREF 0b00001100
//VCC as voltage reference
# define ADC_VREF 0b00000000

#else
//
// ARDUINO 

// Set pin 6's PWM frequency to 62500 Hz (62500/1 = 62500)
// Note that the base frequency for pins 5 and 6 is 62500 Hz  
// *   - Changes on pins 3, 5, 6, or 11 may cause the delay() and
// *     millis() functions to stop working. Other timing-related
#define         P_PWM 5
#define         P_SW 2
#define         P_VCC5 8
#define         A_VFB 0
#define         A_IFB 1

#endif



#endif

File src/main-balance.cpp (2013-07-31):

/**
 * read value from cell, balance if needed, inform the status 
 *  roadmap:
 *  - read value from cell
 *  - get status from stacked cell
 *  - set status from next cell
 * 
 *  
 */


#include <WProgram.h>
#include "config.h"
#include "energy.h"


#ifdef CONFIG_WITH_EEPROM
//#include <EEPROM.h>
#endif



#ifdef CONFIG_WITH_ECLIPSE
extern "C" void __cxa_pure_virtual() {  }
#endif




void setup()   {                
  // initialize the digital pin as VCC
  pinMode(P_SIN, INPUT);     
  digitalWrite(P_SIN, LOW);
  //pinMode(P_SOUT, OUTPUT);     
  //pinMode(P_GND, OUTPUT);     
  //digitalWrite(P_VCC, HIGH);
  //digitalWrite(P_GND, LOW);

  //
  //pullup the AD   
  //pinMode(A_BATTERY, INPUT);
  //digitalWrite(A_BATTERY, HIGH);
  
 



#ifdef CONFIG_WITH_PRINT
  Serial.begin(38400);
	Serial.println("Booting ");
	Serial.print("CPU: ");
	Serial.println(OSCCAL);
#endif

}
 

int o=LOW;

void loop(){		   
	//
	// check if battery is ok
	float vcc=avr_internal_vcc();
	float vtemp=avr_internal_temp();
  int loop=255;
  int pwm=0, dim=0;
#ifdef CONFIG_WITH_PRINT
  energy_debug_on();
	Serial.print(" - Temp. sens: ");
	Serial.println(vtemp,2);
	Serial.print(" - Volt. sens: ");
	Serial.println(vcc,2);
  Serial.println("DEBUG MODE! -- add power +24.3mA");
  energy_debug_off();
#endif  
  while (loop--){
    energy_sleep(100);
  	if (analogRead(2)==LOW)
      digitalWrite(P_SOUT, HIGH);
    else
      digitalWrite(P_SOUT, LOW);
  }
	
}

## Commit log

2013-07-31 first devel board v0.1
    [bicyclelab-charger-1.brd, bicyclelab-charger-1.sch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]
2013-08-18 implement code for tiny and arduino, check Makefile.p328
    [bicyclelab-charger-3.brd, bicyclelab-charger-3.sch]
2013-09-06 clean refactoring of latest tested implementation
    [bicyclelab-charger-4.brd, bicyclelab-charger-4.sch]
2013-09-20 refactor charger code
    [bicyclelab-charger-4.brd, bicyclelab-charger-4.sch]
2013-09-27 prototype is working now. did some adjustement as fine tunning
2013-09-27 power prototype is working now. did some adjustement as fine tunning

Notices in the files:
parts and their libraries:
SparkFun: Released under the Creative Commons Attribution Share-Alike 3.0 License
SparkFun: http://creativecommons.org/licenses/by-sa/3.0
